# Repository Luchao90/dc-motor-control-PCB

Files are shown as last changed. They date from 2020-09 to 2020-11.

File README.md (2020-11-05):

# DC MOTOR CONTROL

This work is realize in context of "pcb design" course from embedded system career FIUBA 2020, for [NOVOTEC](https://www.novotecargentina.com/ofertas.php) company.

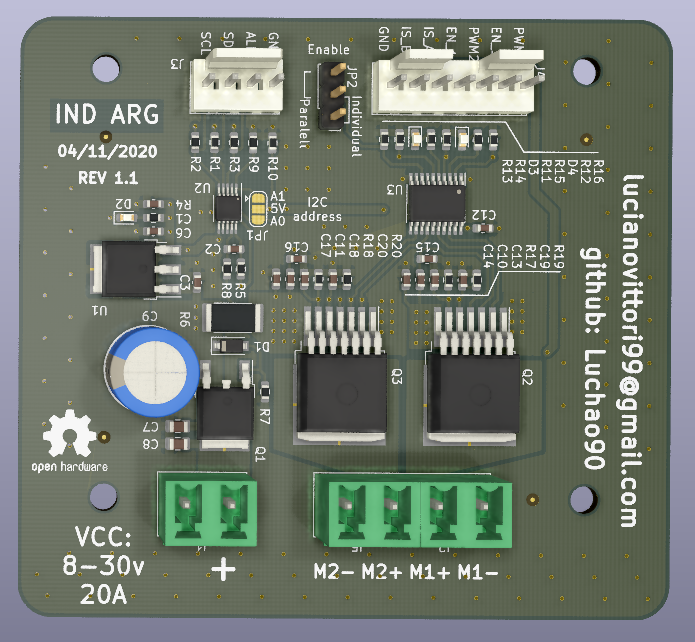
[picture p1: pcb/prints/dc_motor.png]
Pcb-view


# Be careful - NOT TESTED YET.

## SPECS

* Input: 8-30V @30A depends on motor or LOAD.
* PWM Frequency: 30KHz max.
*: 1 DC motor bi directional or 2 DC motor uni directional.
* Alternative: Any kind of PWM control like lamp dimmer for example.
* Control interface: I2C, PWM and ADC.

## Schematic 

[Schematic](pcb/prints/dc_motor.pdf)

Schematic

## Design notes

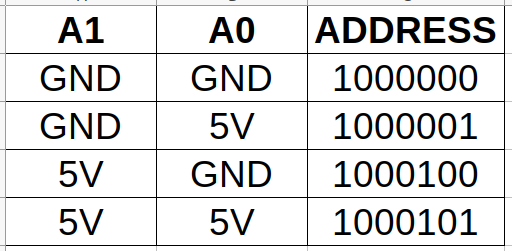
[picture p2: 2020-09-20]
info/ina226-address.png

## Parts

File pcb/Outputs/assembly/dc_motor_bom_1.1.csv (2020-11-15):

Reference | Quantity | Value | Footprint | digikey# | manf#
C1 C2 C3 C6 C12 C14 C17 C19 C20 | 9 | 100nF | Capacitor_SMD:C_0603_1608Metric | 1276-CL10B104KB8WPNDCT-ND | CL10B104KB8WPND
C10 C11 C15 C16 | 4 | 220nF | Capacitor_SMD:C_0603_1608Metric | 311-1830-1-ND | CC0603ZRY5V9BB224
C13 C18 | 2 | 1nF | Capacitor_SMD:C_0603_1608Metric | 399-7842-1-ND | C0603C103M5RACTU
C7 C8 | 2 | 10uF | Capacitor_SMD:C_0805_2012Metric | 490-10505-1-ND | GRM21BC8YA106ME11L
C9 | 1 | 1000uF/35V | Capacitor_THT:CP_Radial_D10.0mm_P5.00mm | 1189-3736-1-ND | 35PK1000MEFCT810X20
D1 | 1 | 10V | Diode_SMD:D_SOD-123 | BZT52C10-FDICT-ND | BZT52C10-7-F
D2 D3 D4 | 3 | Red led 0603 | LED_SMD:LED_0603_1608Metric | 732-4978-1-ND | 150060RS75000
J1 J2 J5 | 3 | Conn_01x02 | Connector_Phoenix_MC_HighVoltage:PhoenixContact_MCV_1,5_2-G-5.08_1x02_P5.08mm_Vertical | 732-2052-ND | 691311500002
J3 | 1 | Conn_01x04 | Connector_Molex:Molex_KK-254_AE-6410-04A_1x04_P2.54mm_Vertical | WM4202-ND | 22232041
J4 | 1 | Conn_01x07 | Connector_Molex:Molex_KK-254_AE-6410-07A_1x07_P2.54mm_Vertical | WM4305-ND | 22053071
JP2 | 1 | EN_Option | Connector_PinHeader_2.54mm:PinHeader_1x03_P2.54mm_Vertical | 732-5316-ND | 61300311121
Q1 | 1 | IPD50P04P4L11 | Package_TO_SOT_SMD:TO-252-2 | 448-IPD50P04P4L11ATMA2CT-ND | IPD50P04P4L11ATMA2
Q2 Q3 | 2 | BTN8962 | Package_TO_SOT_SMD:TO-263-7_TabPin8 | BTN8962TAAUMA1 | BTN8962TAAUMA1INCT-ND
R1 R2 R3 R9 R10 | 5 | 4k7 | Resistor_SMD:R_0603_1608Metric | 311-4.7KGRCT-ND | RC0603JR-074K7L
R17 R18 | 2 | 1k | Resistor_SMD:R_0603_1608Metric | 311-1.00KHRCT-ND | RC0603FR-071KL
R19 R20 | 2 | 470R | Resistor_SMD:R_0603_1608Metric | 311-470HRCT-ND | RC0603FR-07470RL
R4 R11 R12 | 3 | 3k3 | Resistor_SMD:R_0603_1608Metric | 311-3.3KGRCT-ND | RC0603JR-073K3L
R6 | 1 | 10mR | Resistor_SMD:R_2512_6332Metric | CRA2512-FZ-R010ELFCT-ND | CRA2512-FZ-R010ELF
R7 R13 R14 R15 R16 | 5 | 10k | Resistor_SMD:R_0603_1608Metric | 311-10.0KHRCT-ND | RC0603FR-0710KL
R5 R8 | 2 | 10R | Resistor_SMD:R_0603_1608Metric | 311-10.0HRCT-ND | RC0603FR-0710RL
U1 | 1 | L7805 | Package_TO_SOT_SMD:TO-252-3_TabPin2 | 497-1170-1-ND | L7805ABD2T-TR
U2 | 1 | INA226 | Package_SO:VSSOP-10_3x3mm_P0.5mm | 296-29034-1-ND | INA226AIDGSR
U3 | 1 | 74AHC244 | Package_SO:TSSOP-20_4.4x6.5mm_P0.65mm | 296-SN74AHC244QPWRQ1CT-ND | SN74AHC244QPWRQ1

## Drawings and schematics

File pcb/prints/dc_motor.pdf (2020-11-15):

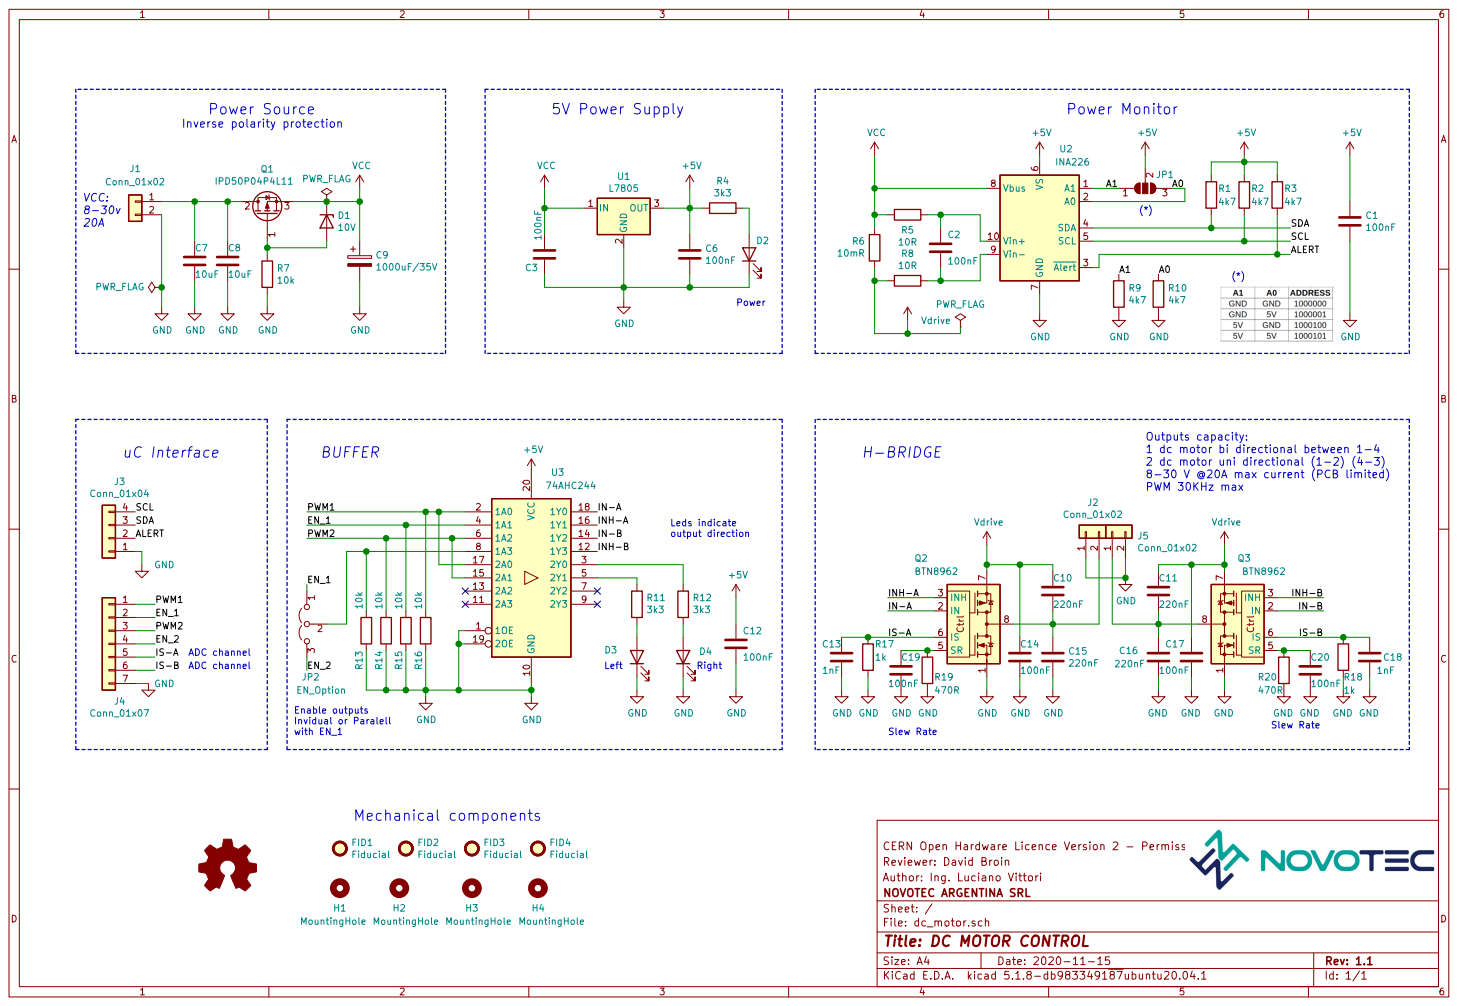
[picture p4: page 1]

2 dc motor uni directional (1-2) (4-3)

8-30 V @20A max current (PCB limited) PWM 30KHz max Mechanical components

File: dc_motor.sch Sheet: / NOVOTEC ARGENTINA SRL Author: Ing. Luciano Vittori Reviewer: David Broin CERN Open Hardware Licence Version 2 - Permissive H1 MountingHole

Id: 1/1 Title: DC MOTOR CONTROL

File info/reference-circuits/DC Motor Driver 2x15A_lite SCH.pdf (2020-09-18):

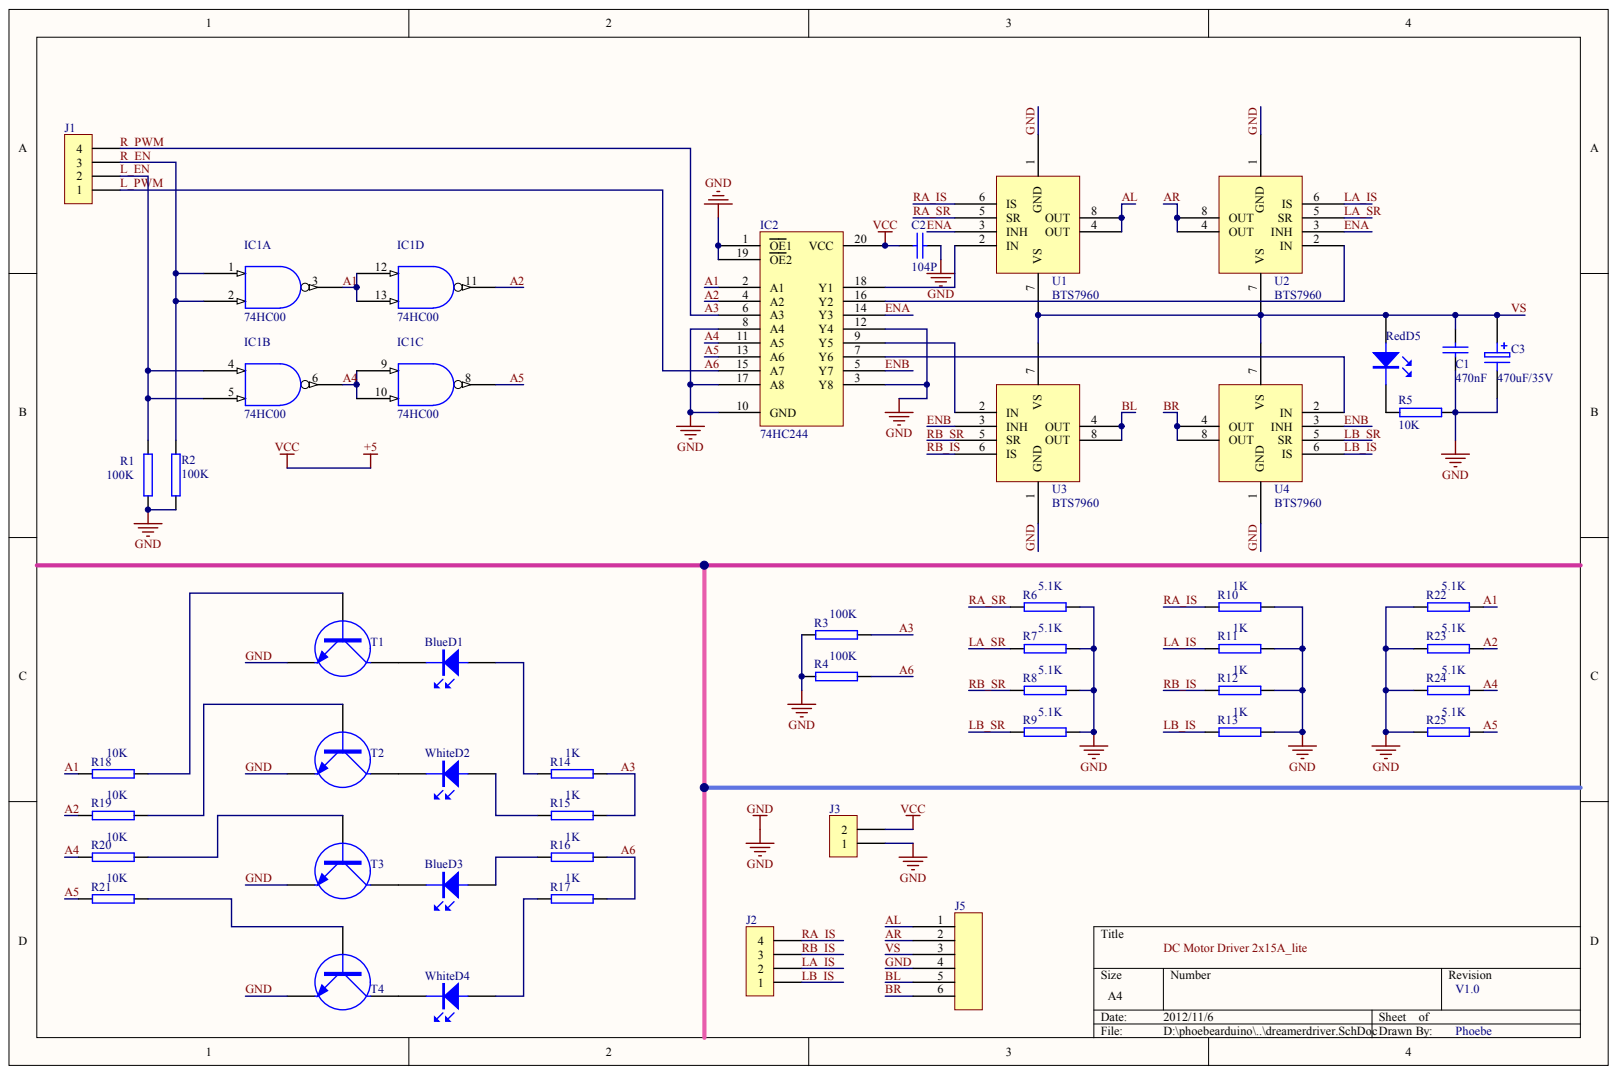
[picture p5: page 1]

R_EN
L_EN

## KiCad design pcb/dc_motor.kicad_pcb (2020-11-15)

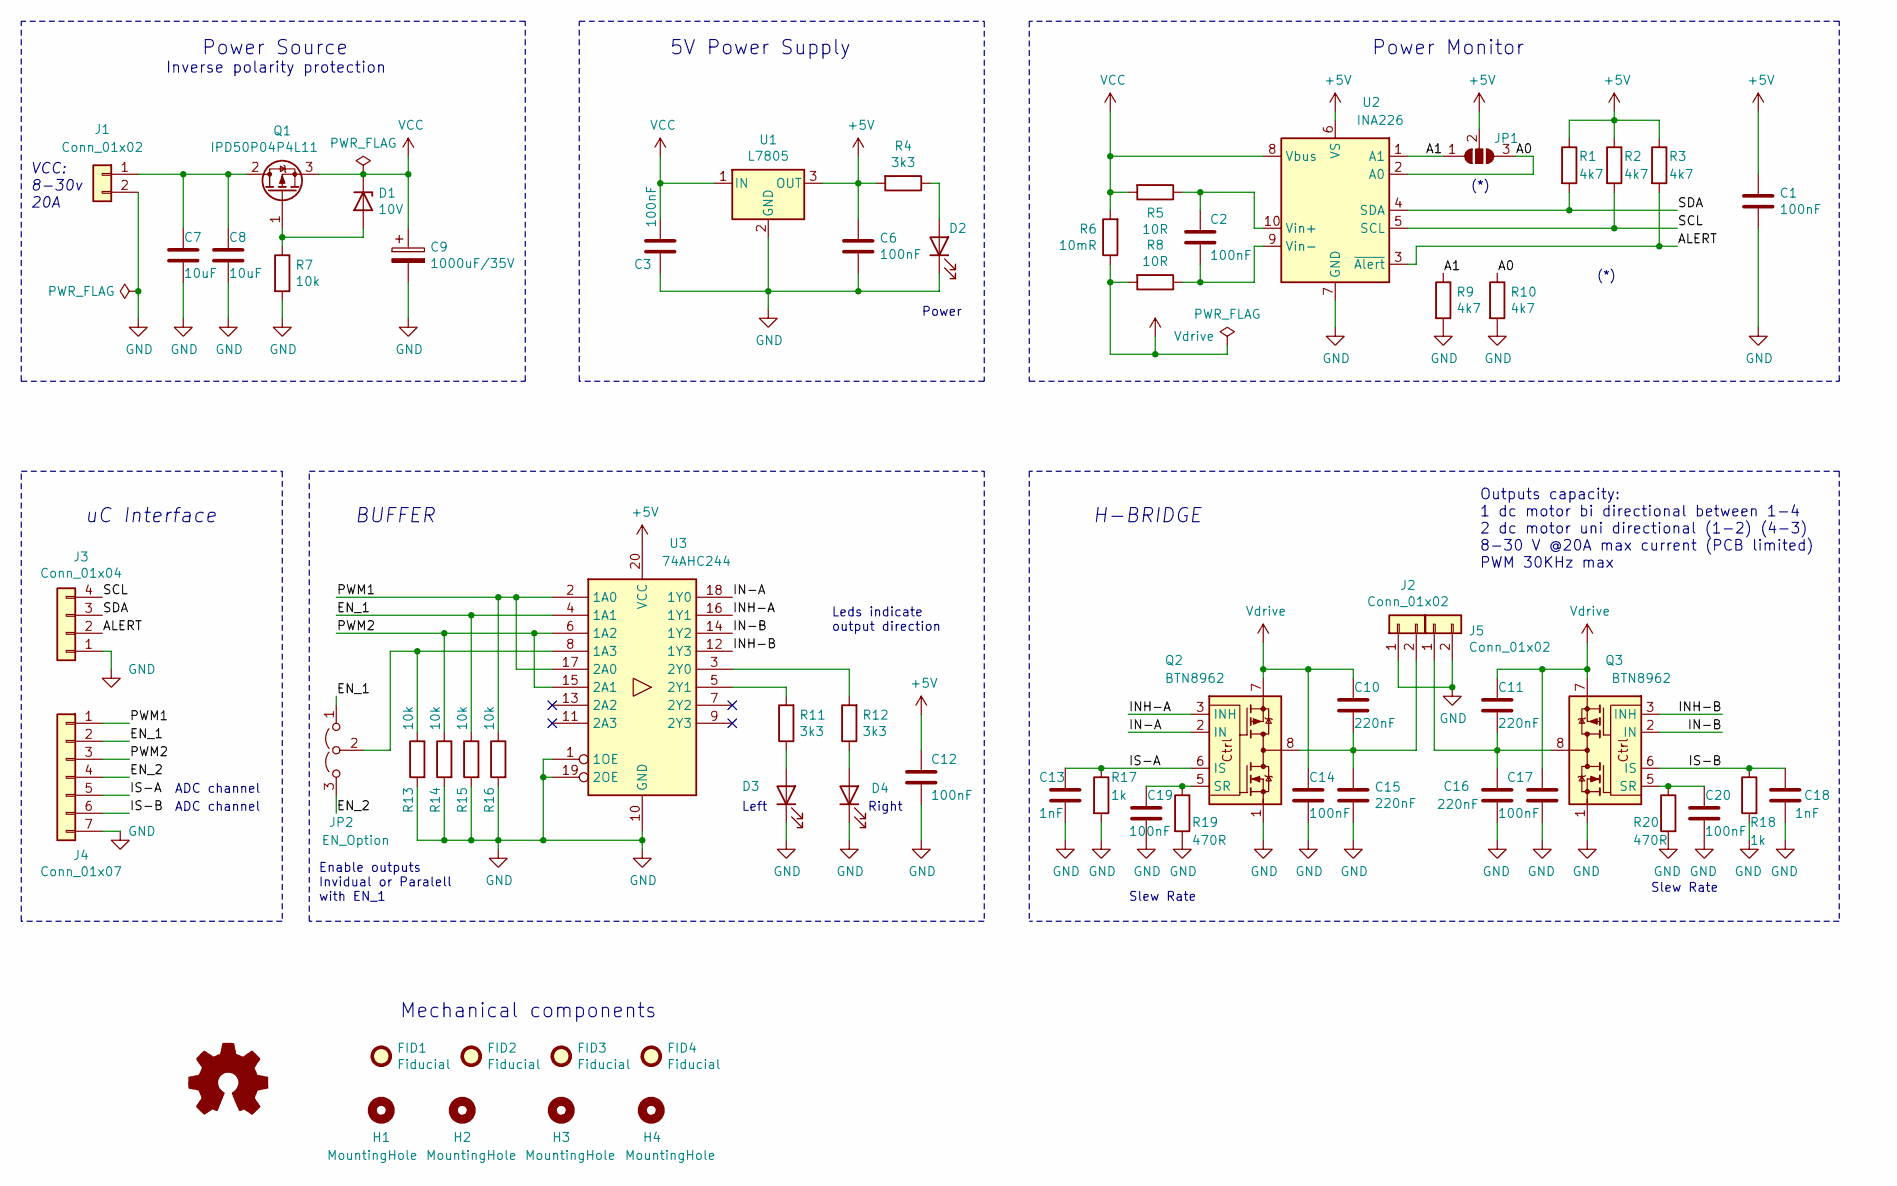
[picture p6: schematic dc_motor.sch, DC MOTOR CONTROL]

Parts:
C1, C2, C3, C6, C12, C14, C17, C19, C20: 100nF; C_0603_1608Metric; digikey# 1276-CL10B104KB8WPNDCT-ND
C7, C8: 10uF; C_0805_2012Metric; digikey# 490-10505-1-ND
C9: 1000uF/35V; CP_Radial_D10.0mm_P5.00mm; digikey# 1189-3736-1-ND
C10, C11, C15, C16: 220nF; C_0603_1608Metric; digikey# 311-1830-1-ND
C13, C18: 1nF; C_0603_1608Metric; digikey# 399-7842-1-ND
D1: 10V; D_SOD-123; digikey# BZT52C10-FDICT-ND
D2, D3, D4: Red led 0603; LED_0603_1608Metric; digikey# 732-4978-1-ND
FID1, FID2, FID3, FID4: Fiducial; Fiducial_0.5mm_Mask1.5mm; digikey# dnp
H1, H2, H3, H4: MountingHole; MountingHole_3.2mm_M3_ISO14580; digikey# dnp
J1, J2, J5: Conn_01x02; PhoenixContact_MCV_1,5_2-G-5.08_1x02_P5.08mm_Vertical; digikey# 732-2052-ND
J3: Conn_01x04; Molex_KK-254_AE-6410-04A_1x04_P2.54mm_Vertical; digikey# WM4202-ND
J4: Conn_01x07; Molex_KK-254_AE-6410-07A_1x07_P2.54mm_Vertical; digikey# WM4305-ND
JP1: SolderJumper_3_Open; SolderJumper-3_P1.3mm_Open_RoundedPad1.0x1.5mm; digikey# dnp
JP2: EN_Option; PinHeader_1x03_P2.54mm_Vertical; digikey# 732-5316-ND
LOGO1: Logo_Open_Hardware_Small; OSHW-Logo2_9.8x8mm_SilkScreen; digikey# dnp
Q1: IPD50P04P4L11; TO-252-2; digikey# 448-IPD50P04P4L11ATMA2CT-ND
Q2, Q3: BTN8962; TO-263-7_TabPin8; digikey# BTN8962TAAUMA1
R1, R2, R3, R9, R10: 4k7; R_0603_1608Metric; digikey# 311-4.7KGRCT-ND
R4, R11, R12: 3k3; R_0603_1608Metric; digikey# 311-3.3KGRCT-ND
R5, R8: 10R; R_0603_1608Metric; digikey# 311-10.0HRCT-ND
R6: 10mR; R_2512_6332Metric; digikey# CRA2512-FZ-R010ELFCT-ND
R7, R13, R14, R15, R16: 10k; R_0603_1608Metric; digikey# 311-10.0KHRCT-ND
R17, R18: 1k; R_0603_1608Metric; digikey# 311-1.00KHRCT-ND
R19, R20: 470R; R_0603_1608Metric; digikey# 311-470HRCT-ND
U1: L7805; TO-252-3_TabPin2; digikey# 497-1170-1-ND
U2: INA226; VSSOP-10_3x3mm_P0.5mm; digikey# 296-29034-1-ND
U3: 74AHC244; TSSOP-20_4.4x6.5mm_P0.65mm; digikey# 296-SN74AHC244QPWRQ1CT-ND

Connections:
+5V: C1.1, C6.1, C12.1, JP1.2 (C), R1.1, R2.1, R3.1, R4.2, U1.3 (OUT), U2.6 (VS), U3.20 (VCC)
/A0: JP1.3 (B), R10.1, U2.2 (A0)
/A1: JP1.1 (A), R9.1, U2.1 (A1)
/ALERT: J3.2, R3.2, U2.3 (~Alert~)
/EN_1: J4.2, JP2.1 (A), R15.1, U3.4 (1A1)
/EN_2: J4.4, JP2.3 (B)
/IN-A: Q2.2 (IN), U3.18 (1Y0)
/IN-B: Q3.2 (IN), U3.14 (1Y2)
/INH-A: Q2.3 (INH), U3.16 (1Y1)
/INH-B: Q3.3 (INH), U3.12 (1Y3)
/IS-A: C13.1, J4.5, Q2.6 (IS), R17.1
/IS-B: C18.1, J4.6, Q3.6 (IS), R18.1
/PWM1: J4.1, R16.1, U3.2 (1A0), U3.17 (2A0)
/PWM2: J4.3, R14.1, U3.6 (1A2), U3.15 (2A1)
/SCL: J3.4, R2.2, U2.5 (SCL)
/SDA: J3.3, R1.2, U2.4 (SDA)
GND: C1.2, C3.2, C6.2, C7.2, C8.2, C9.2, C12.2, C13.2, C14.2, C15.2, C16.2, C17.2, C18.2, C19.2, C20.2, D2.1 (K), D3.1 (K), D4.1 (K), J1.2, J2.1, J3.1, J4.7, J5.2, Q2.1, Q3.1, R7.2, R9.2, R10.2, R13.2, R14.2, R15.2, R16.2, R17.2, R18.2, R19.2, R20.2, U1.2 (GND), U2.7 (GND), U3.1 (1OE), U3.10 (GND), U3.19 (2OE)
unnamed: C2.1, R5.1, U2.10 (Vin+)
unnamed: C2.2, R8.1, U2.9 (Vin-)
unnamed: C7.1, C8.1, J1.1, Q1.2 (D)
unnamed: C10.2, C15.1, J2.2, Q2.4, Q2.8
unnamed: C11.2, C16.1, J5.1, Q3.4, Q3.8
unnamed: C19.1, Q2.5 (SR), R19.1
unnamed: C20.1, Q3.5 (SR), R20.1
unnamed: D1.2 (A), Q1.1 (G), R7.1
unnamed: D2.2 (A), R4.1
unnamed: D3.2 (A), R11.1
unnamed: D4.2 (A), R12.1
unnamed: JP2.2 (C), R13.1, U3.8 (1A3)
unnamed: R11.2, U3.5 (2Y1)
unnamed: R12.2, U3.3 (2Y0)
VCC: C3.1, C9.1, D1.1 (K), Q1.3 (S), R5.2, R6.2, U1.1 (IN), U2.8 (Vbus)
Vdrive: C10.1, C11.1, C14.1, C17.1, Q2.7, Q3.7, R6.1, R8.2

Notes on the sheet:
H-BRIDGE
Inverse polarity protection
Power Source
Power Monitor
(*)
5V Power Supply
BUFFER
Mechanical components
Outputs capacity: 1 dc motor bi directional between 1-4 2 dc motor uni directional (1-2) (4-3) 8-30 V @20A max current (PCB limited) PWM 30KHz max
ADC channel
uC Interface
VCC: 8-30v 20A
Leds indicate output direction
Slew Rate
Enable outputs Invidual or Paralell with EN_1
Power
Left
Right

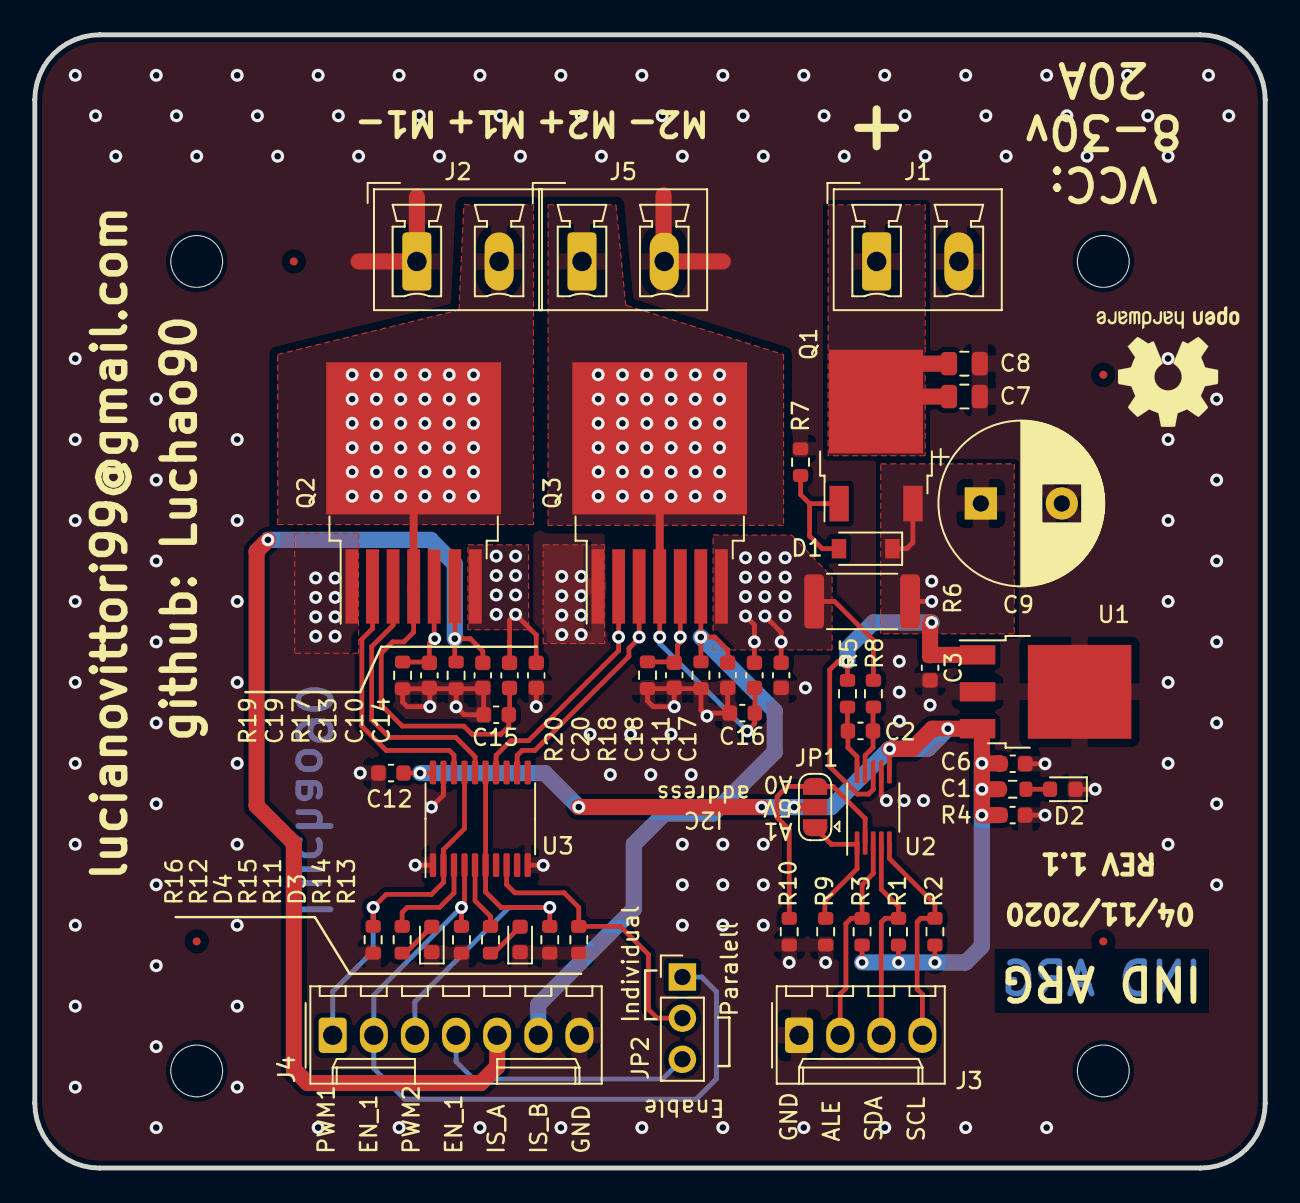
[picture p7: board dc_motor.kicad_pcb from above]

Board: 2 copper layers, 76.0 x 70.0 mm, 64 parts (0 on the bottom side), 33 nets.

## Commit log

2020-09-18 project folder
    [dc_motor.kicad_pcb, dc_motor.sch]
2020-09-19 schematics without values and footprint yet
2020-09-20 sch values
    [dc_motor.sch]
2020-10-09 Sch complete.
    first revision.
    [dc_motor.kicad_pcb, dc_motor.sch]
2020-10-16 Part number changes
    [dc_motor.kicad_pcb, dc_motor.sch]
2020-10-16 Rev1
    Correcciones de primera revisión del profesor, hasta el esquemático.
    [dc_motor.kicad_pcb, dc_motor.sch]
2020-11-01 board dimension
    change 1 capacitor value.
    [dc_motor.kicad_pcb, dc_motor.sch]
2020-11-01 routing 01
    [dc_motor.kicad_pcb]
2020-11-01 pcb 01
    [dc_motor.kicad_pcb]
2020-11-02 fix unconnected
    [dc_motor.kicad_pcb]
2020-11-04 Diego reviews 1
    [dc_motor.kicad_pcb]
2020-11-04 add open hardware logo
    [dc_motor.kicad_pcb, dc_motor.sch]
2020-11-04 add outputs fab
    [dc_motor-B_Cu.gbr, dc_motor-B_Mask.gbr, dc_motor-Dwgs_User.gbr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]
2020-11-04 schematic print
2020-11-05 interactive component place
    [dc_motor.sch]
2020-11-05 change gitignore for BOM
2020-11-05 symbols field
    [dc_motor.sch]
2020-11-05 add BOM
2020-11-05 prints place
2020-11-14 change #digikey to digikey#
    [dc_motor.sch]
2020-11-14 csv BOM
    [dc_motor.csv, dc_motor.xml]
2020-11-14 kibom update
    [dc_motor.xml]
2020-11-15 economic BOM
    [dc_motor-B_Cu.gbr, dc_motor-B_Mask.gbr, dc_motor-Dwgs_User.gbr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]
2020-11-15 Rev 1.1
    Change power connectors and limited current to 20A
    [dc_motor-B_Cu.gbr, dc_motor-B_Mask.gbr, dc_motor-Dwgs_User.gbr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]
